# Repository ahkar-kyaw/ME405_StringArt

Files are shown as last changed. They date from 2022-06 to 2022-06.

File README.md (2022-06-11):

<!---
<img src="media/1.gif" alt="" width="200"/>
<img src="media/2.gif" alt="" width="200"/>
<img src="media/3.gif" alt="" width="200"/>
<img src="media/4.gif" alt="" width="200"/>

<img src="media/2.jpg" alt="" width="200"/>
<img src="media/3.jpg" alt="" width="200"/>
<img src="media/1.jpeg" alt="Cat_Original" width="200"/>
<img src="media/4.jpg" alt="Cat_String" width="200"/>
<img src="media/5.jpg" alt="" width="200"/>
<img src="media/6.jpg" alt="" width="200"/>
<img src="media/7.jpg" alt="" width="200"/>
<img src="media/8.jpg" alt="" width="200"/>
<img src="media/9.jpg" alt="" width="200"/>
<img src="media/10.jpg" alt="" width="200"/>

![](media/8.jpg)
![](media/9.jpg)
![](media/10.jpg)
-->

<p align="center">
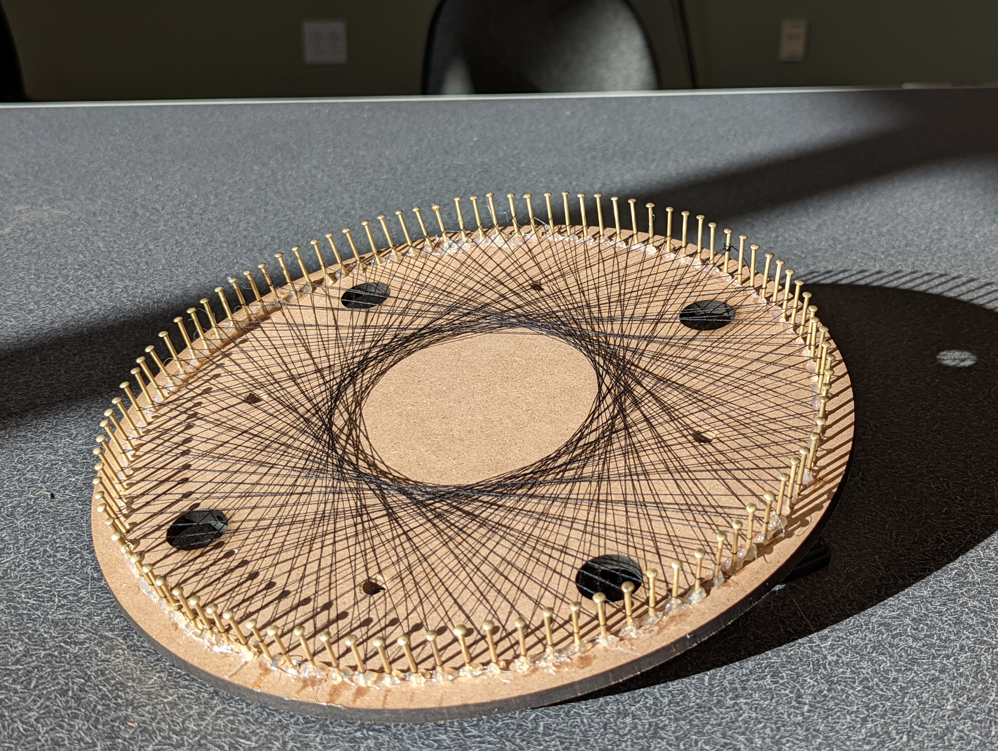
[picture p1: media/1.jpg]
  
</p>

<div align="center">
  <h1>String Art Machine</h1>
  <p><strong>By:</strong> Ahkar Kyaw, Elvis Tang</p>
</div>

In this tutorial we will learn how to build a machine that can replicate an image using strings. We built this machine for our ME405 class. It is still a work in progress with many rooms for improvement but we are very pleased with how far it has come and we are excited to share the project with you. 

# Introduction
String art, often referred to as pin-and-thread art, is a form of art that weaves colored string, wool, wire, or yarn between hammered nails to make geometric patterns. String art is not new and its origins go all the way back to the 19th century. It started off as an educational tool to introduce mathematical ideas to children but came back in the late 1960s as a decorative craft in a form of books and kits. 

Inspired by the beauty and complexity of this art style, we decided that we want to build a machine that can replicate any image using lines and recreate it physically in a form of string art. This was a very challenging project and due to time constraint, we were unable to perfect it to our desired standard. However, it works and we are thrilled to share our project with you. Hopefully you will be inspired to recreate a project like this yourself. 

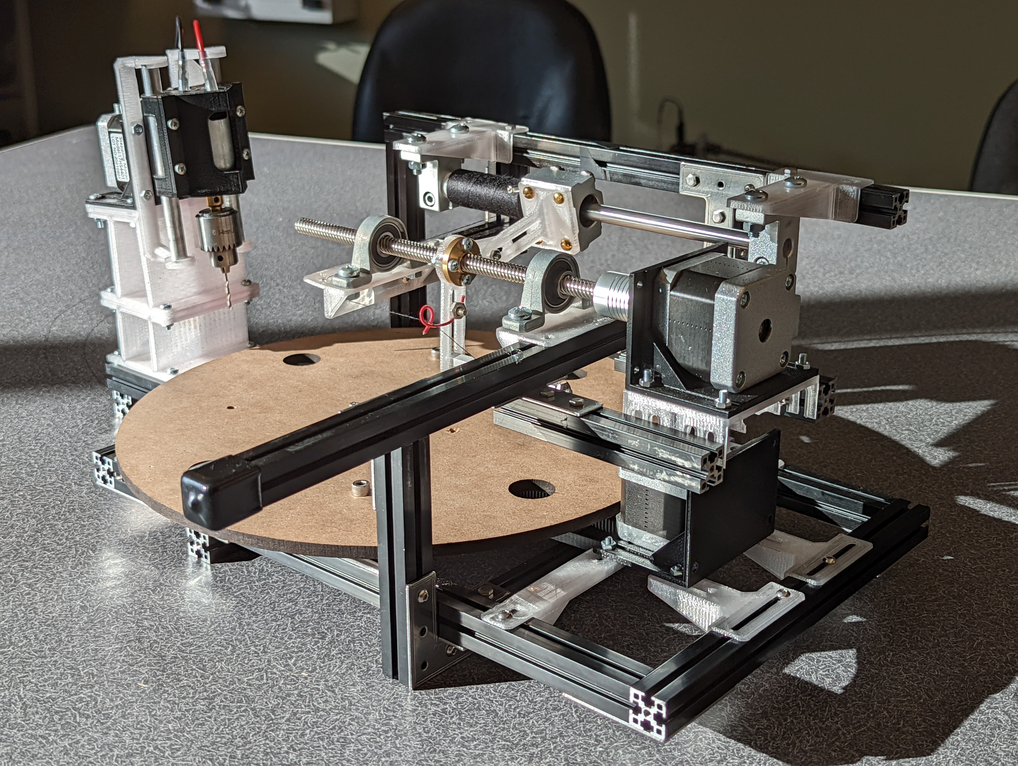
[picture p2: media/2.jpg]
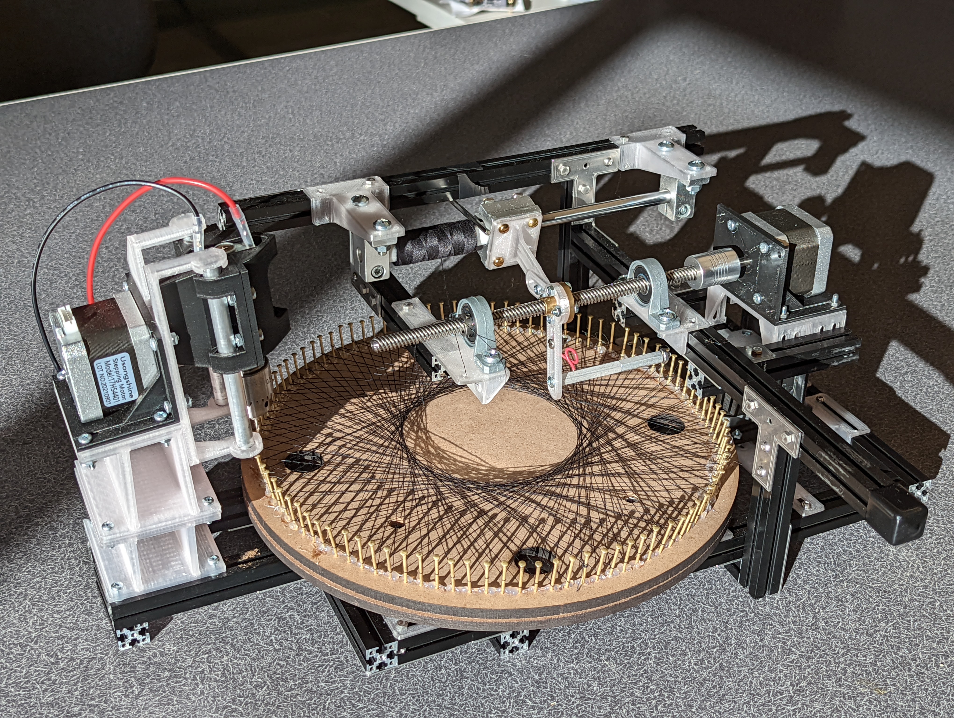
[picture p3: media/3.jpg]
|  | |
| --- | --- |

# Product Specification
## Hardware Components
| **Components** | **vender** | **Dimension** |
| :---:  | :---: | :---: |
| MDF board | [Amazon](https://www.amazon.com/dp/B07QWSTMWJ?ref_=cm_sw_r_cp_ud_dp_WGG48NSVNE196GH4DMZJ) | 14-in(L) x 11-in(W) x 0.25-in(T)|
| Nails | [Amazon](https://www.amazon.com/Projects-Antique-Repairing-Decorative-Accessories/dp/B082J2JXZD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) | 23mm(L) |
| String | [Amazon](https://www.amazon.com/dp/B07LC1YDVR?ref_=cm_sw_r_cp_ud_dp_Z0H458M8TY3VP6MC05YG) | 200m |
| 80/20 Aluminum Extrusion | [McMASTER-CARR](https://www.mcmaster.com/80//t-slotted-framing-rails/) | 20mm x 20mm |
| T8 Lead Screw Nut Set | [Amazon](https://www.amazon.com/dp/B07GV72326?ref_=cm_sw_r_cp_ud_dp_XBR2BX6C1A7YK6SPVKN0) | 200mm(L), 8mm(D) |

## Electronic Components
| **Components** | **Vender** | **Datasheet**  |
| :---:  | :---: | :--- |
| NUCLEO (STM32L476RG) | [MOUSER](https://www.mouser.com/ProductDetail/STMicroelectronics/NUCLEO-L476RG?qs=PRtH0mD6DWbM6mRV5DKjBQ%3D%3D) | https://www.st.com/resource/en/datasheet/stm32l476rg.pdf |
| Shoe of Brian | [OSHPARK](https://oshpark.com/shared_projects/e6X6OnYK) |  http://wind.calpoly.edu/ME405/doc/shoe_info.html |
| Mini Hand Drill DC Motor | [Amazon](https://www.amazon.com/AUTOTOOLHOME-Electric-Drill-Motor-Drills/dp/B01LZYWFE4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)| https://www.sears.com/autotoolhome-mini-dc-12v-electric-hand-drill-motor/p-A098205228 |
| NEMA 17 Stepper Motor | [Amazon](https://www.amazon.com/dp/B07QV1ZVJR?tag=rpantiques-20&linkCode=ogi&th=1) | http://www.autoflexible.com/file_upload/product/attach/NEMA%2017.pdf |
| LCD 1602 (I2C port) | [Amazon](https://www.amazon.com/dp/B019K5X53O?ref_=cm_sw_r_cp_ud_dp_NDRGXARM7KG02A7N59Y2) | http://www.handsontec.com/dataspecs/module/I2C_1602_LCD.pdf |
| TMC4210 | [MOUSER](https://www.mouser.com/ProductDetail/Trinamic/TMC4210-I?qs=TiOZkKH1s2TH5TqjeGBn1g%3D%3D) | https://www.trinamic.com/fileadmin/assets/Products/ICs_Documents/TMC4210_Datasheet_Rev.1.06.pdf |
| TMC2208 | [Amazon](https://www.amazon.com/Printer-TMC2208-Screwdriver-Controller-Ramps1-4/dp/B082LSQWZF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) | https://www.trinamic.com/fileadmin/assets/Products/ICs_Documents/TMC220x_TMC2224_datasheet_Rev1.09.pdf |

## Manufacturing / Machining Tools
| **Tool** | Source Files |
| :---:  | :---:  |
| 3D Printer | [ME405_StringArt/CAD Files/3D Printing/](https://github.com/AhKyaw/ME405_StringArt/tree/main/CAD%20Files/3D%20Printing) |
| Laser Cutter | [ME405_StringArt/CAD Files/Laser Cutting/](https://github.com/AhKyaw/ME405_StringArt/tree/main/CAD%20Files/Laser%20Cutting)  |

# System Design
## Mechanical Design
To begin with, let’s take a look at the mechanical components of this machine. The overall frame of this machine is made entirely out of 80/20 aluminum extrusion. The machines moves using 3 stepper motors and a DC motor with a drill attached to the tip. These motors are then mounted onto the frame using custom 3D printed parts. CAD files for these 3D printed parts can be found under Manufacturing - 3D Printer Source files. 

For the drawing board, we used a laser cut MDF board. The DXF file for laser cutting can be found under Manufacturing - Laser Cutter Source files. Once the board is cut, we attached it onto the 3D printed braket #4 and the lazy susan, which will be attached to the machine's frame. For the art canvas we want it to be easily removeable so we mounted another similar MDF board onto this existing platform using the pre-cut alignmnet holes. 

The full CAD model for the assembly of the machine can be found in the CAD folder under our GitHub Repository. 

<div align="center">
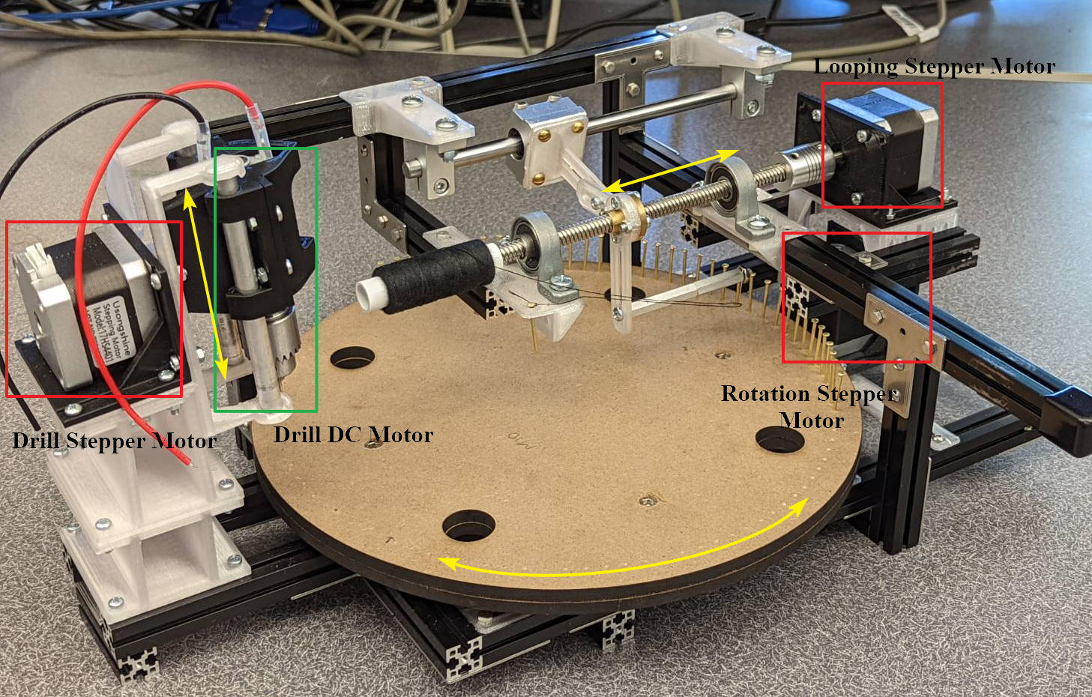
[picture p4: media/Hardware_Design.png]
Hardware_Design
  
</div>

## System Operating Procedure
<p>The figure below shows how the string art machine works. First, we need to convert the image to string art and generate its pin sequence via the Python file StringArt_Gen.py on our computer. After the pin sequence is generated, we will transfer this data to the Nucleo STM32 board. And based on the finite state machine and pin sequence, the Nucleo board will communicate with the motor driver through the SPI protocol and further control the motor to perform desired actions.</p>
<div align="center">
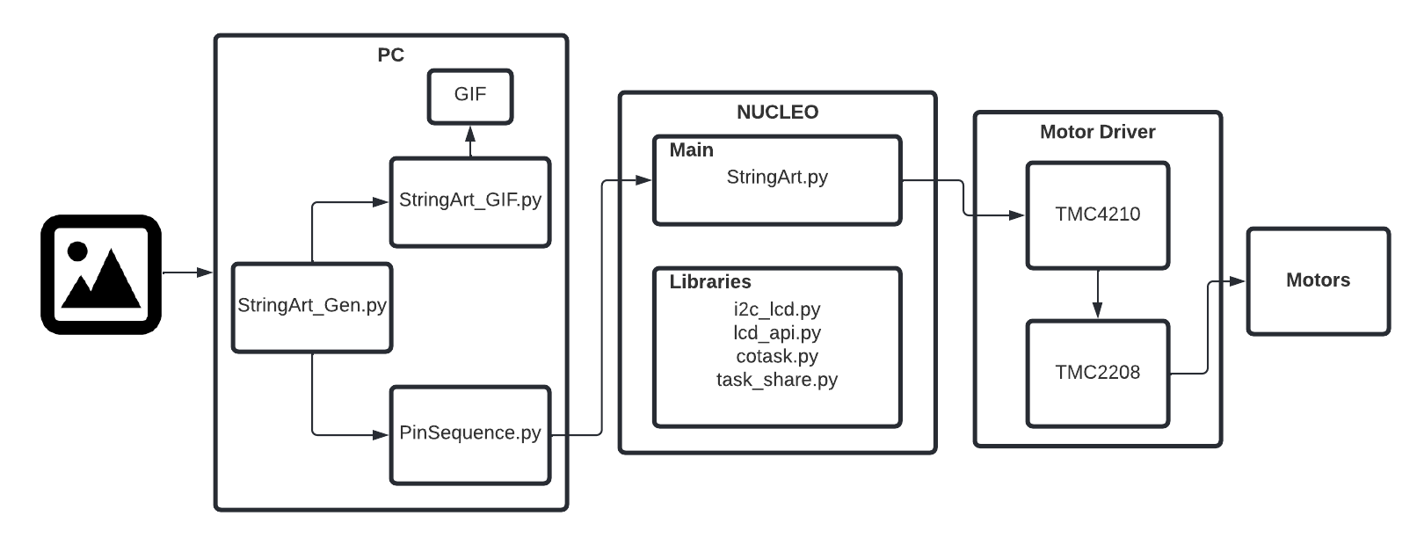
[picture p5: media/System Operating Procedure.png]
  
</div>

## Software Design
### String Art Generator
Our current StringArt_Gen.py file is heavily based on this github repository: [kaspermeerts/stringart.py](https://gist.github.com/kaspermeerts/781f0137b361b51224dcab722ae387b4), and also the knowledge in this paper: [String Art: Towards Computational Fabrication of String Images](https://www.dmg.tuwien.ac.at/geom/ig/publications/stringart/stringart.pdf).
<p>The two figures below show the image before and after string art conversion. And before we input the image into the string art generator, we need to crop the image into square shape to make the program run normally.</p>

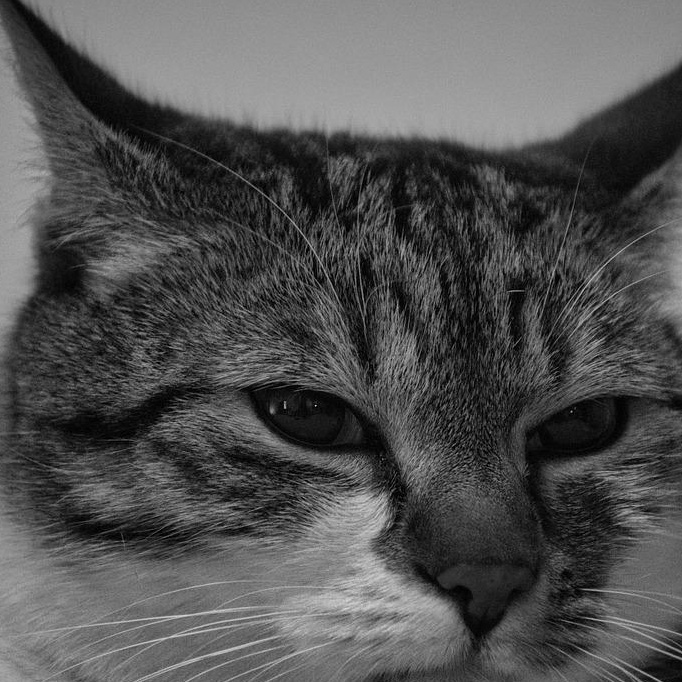
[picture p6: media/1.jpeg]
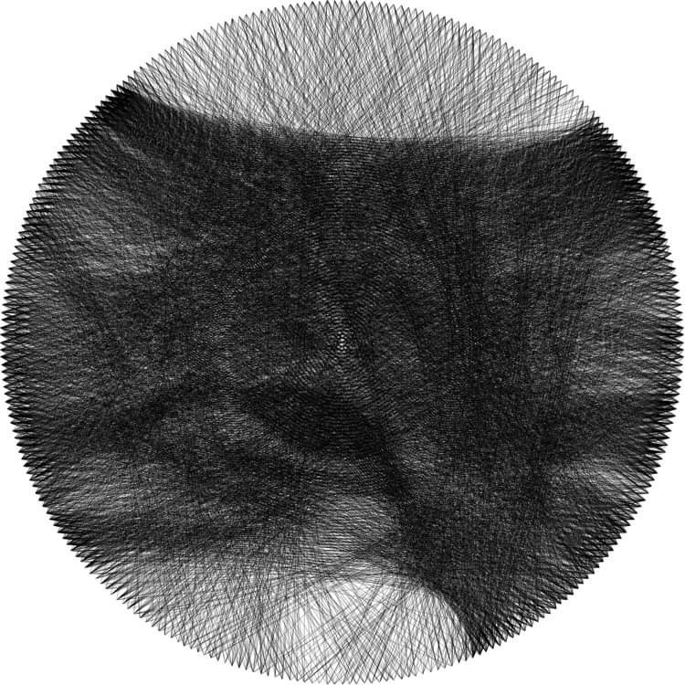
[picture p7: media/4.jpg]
|  |  |
| :---: |:---:|
| Original Image | String Art |

## Firmware Design
### Finite State Machine

<div align="center">
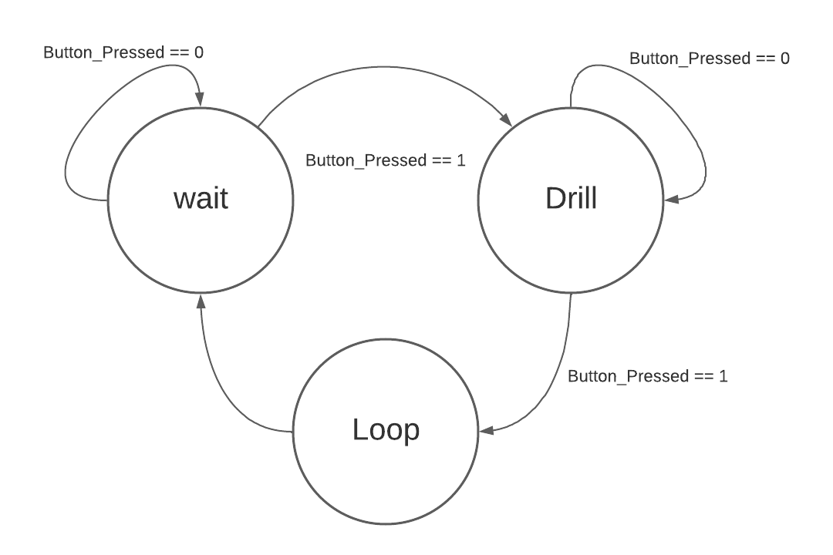
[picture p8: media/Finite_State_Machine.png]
  
</div>

There are a total of three states in this project. The first state is the wait state, in this state the system will initiate the motor setup and wait until the button is pressed. After pressing the button, the system enters the drilling state.</br>

In the drilling state, there are three subroutines, the board rotates to the desired pin, the drill stepper motor rolls the DC drilling motor down to drill holes in the board, and lifts the DC motor up after drilling to the desired depth. The system will loop through these subroutines until there are holes in all desired nail locations. Because we need to put the nails into the holes manually, the system will stay inside the drilling state till we finish inserting nails onto the board and press the button.</br> 

While finishing inserting the nails and pushing the button, the system will enter the looping state. There are four subroutines in the looping state, first, the board will rotate to the degree of desired nails + theta (theta is half of the degree difference between the two nails), and the needle will move outside the edge of the circle that constructs by the nails. After the needle moves outside the circle, the board will rotate to the degree of desired nails - theta. And the needle will move back inside the circle. These are the four subroutines that the system keeps looping through till the maximum number of lines is achieved.</br> 

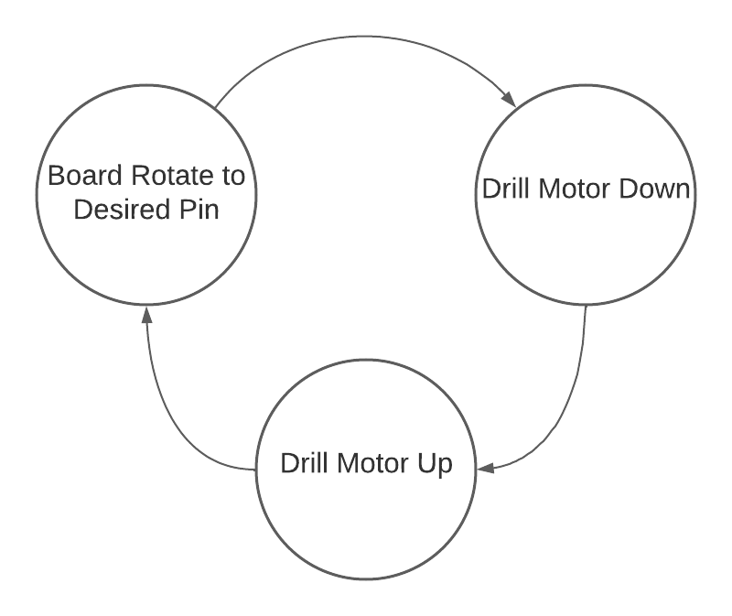
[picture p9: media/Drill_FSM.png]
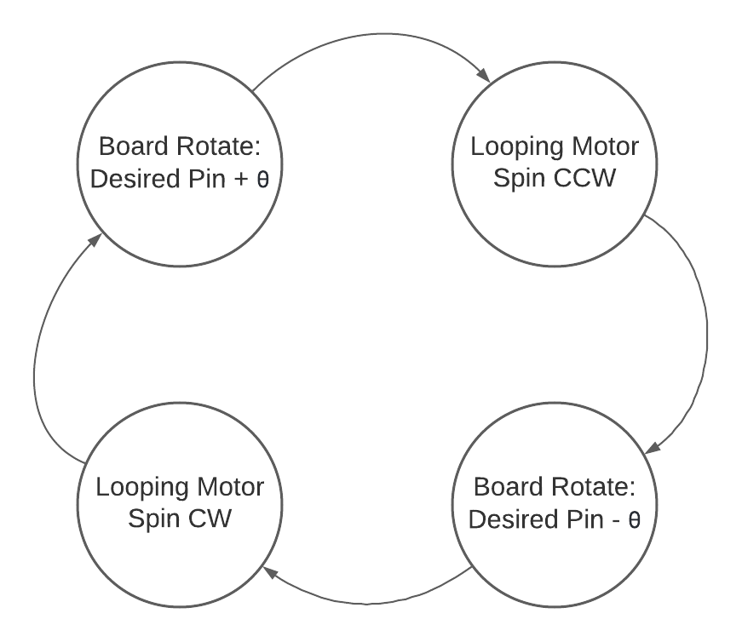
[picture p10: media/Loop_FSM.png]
|  |  |
| :---: |:---:|
| Drilling State | Loop State |

## Motor Control

We use TMC4210 and TMC2208 as our motion controller and motor driver. STM32 will communicate with the TMC4210 through the SPI protocols, and TMC4210 will generate respective steps and direction signals to TMC2208. After the TMC2208 receives those two signals, it will send the respective power to the motor and the motor will do the desired action.

<div align="center">
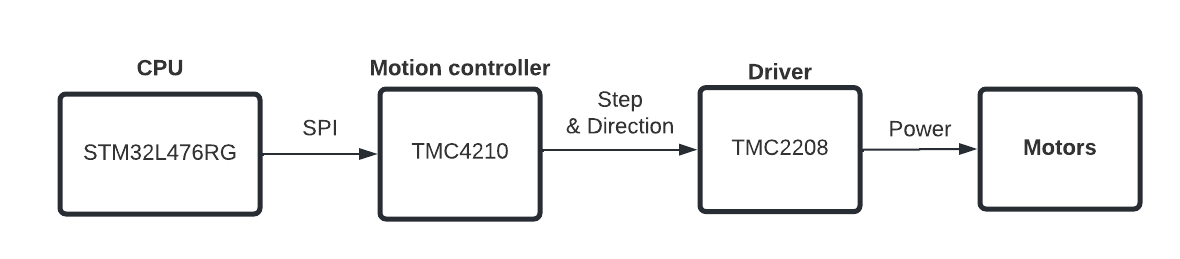
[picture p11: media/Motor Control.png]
  
</div>

# Results Demonstration
Here you will see our machine in action. There are 3 main stages to making a string art on this machine. First stage involves drilling holes for the nails to be slotted in and we call it the drilling stage. The second stage is where you manually put nails into these holes and attaching the string onto one of the nail. We call this stage a nailing stage. Last but not least, we have the looping stage where the needle move around and spin the board to loop the strings around the nails.

## Drilling
What you see below is a short timelapse of the machine drilling a hole and spinning the board around one step at a time. 



## Nailing
This is a very simple and manual stage where you manually put nails into each holes that the machine just drilled. Ideally, the holes will be deep enough such that they will be strong and stable to withstand the tension created by the string. However, we bought a quarter inch MDF board for our project and it turns out, quarter inch was insufficient to withstand the load so we had to go an extra step and used some hot-glue to make the base contact a little stronger. After all the nails are slotted in, tie the end of the string onto one of the nail and position this nail directly under the needle. Ideally, we want to use limit switches so that the alignment process is automated. For now, we manually aligned the first nail with the needle tip. 

## Looping
### Without Interference
The gif you see below is a short timelapse of the machine looping the string around the nails without any human interference. It is pretty successful for the most part but as you can see, on the sixth loop, the nail was a little shorter than the designed height so the string slipped out, forcing us to restart the machine. 



### Mechanism
| This is a close up, real-time video showing how the needle and the strings are attached such that it can loop around the nail without getting tangled up.  |  | 
| :--- |:---|

# Challenges
Due to our lack of experience developing mechanical systems and budget constraint, most of the problems for the project arises in the mechanical side of the design. Since this is the first time developing such complex mechanical system for both of us, we spent too much time getting things right in the designing stage. We designed many of the parts from bottom up and that cost us a lot of time. By the time we finished a prototype to test with the program, we only have two weeks left. Therefore, we did not have much time to buy new parts and redesign the system to fix the problems. Ideally, we should have focused on getting the mechanical design ready using off the shelf components as early as possible so that we get more time to perfect the design. 

### Inconsistent Nail Height:<br>

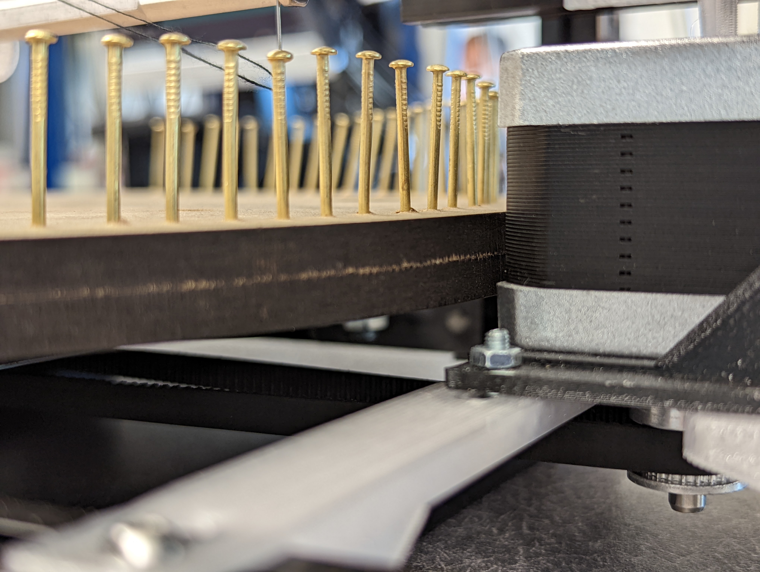
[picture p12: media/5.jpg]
|  | The first problem we encountered was the height inconsistency among the nails that we purchased. Even though we managed to drill all the holes to be exactly the same depth, the point of contact between each nail and the looping needle is different. Therefore, the string occasionally slip over the top if the nail is too short compared to others. To fix this problem, you need an alternative string feeding mechanism where the string is fed directly from the top instead of the side like what we have. This way, you the needle can loop the strings along a much lower plane without having to worry about the string getting tangled up. |
| --- |:---|

### String Getting Tangled Up:<br>
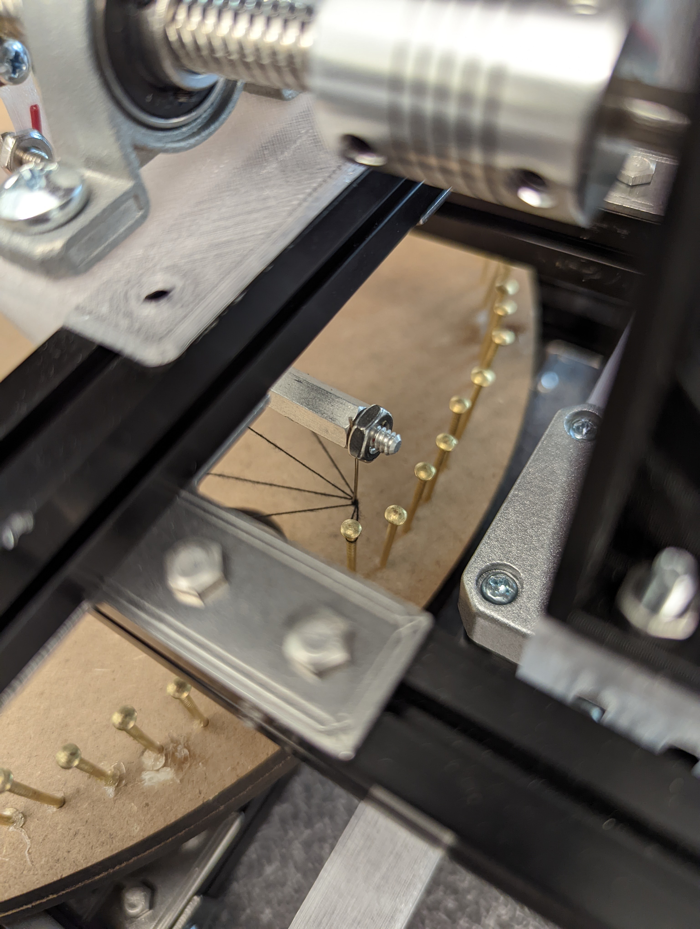
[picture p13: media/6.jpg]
|  | The second problem we encountered was with regards to the string getting tangled up after looping around the nail. There are two main reasons for why this happen. First is due to the lack of tension and retraction system for the string. This causes the string to droop down after the needle pulls the string to loop around the nail everytime. When the board rotates after, the loose part causes the strings to get tangled up. To fix this problem, you could modify the string feeding system so that it goes through several pulley to maintain the tension in the string. You could also add a retraction system to the spool of string so that it will prevent the string from drooping down after pulling it too far. The second reason is due to the nails not being slanted enough. We knew all along that if all the strings loop around along the same height, it will cause them to crash with each other causing the stings to get tangled up when rotating the board. Therefore, we tiltted the drill bit to be at a 5 degrees angle from the vertical, hoping that the slope will cause the strings to slide down the nail after each loop. However, the slope was not steep enough, causing the strings to get tangled up. For future development, the drill should be angled at least 10 degrees from the vertical. |
| --- |:---|

### Insufficient Nail Depth:<br>
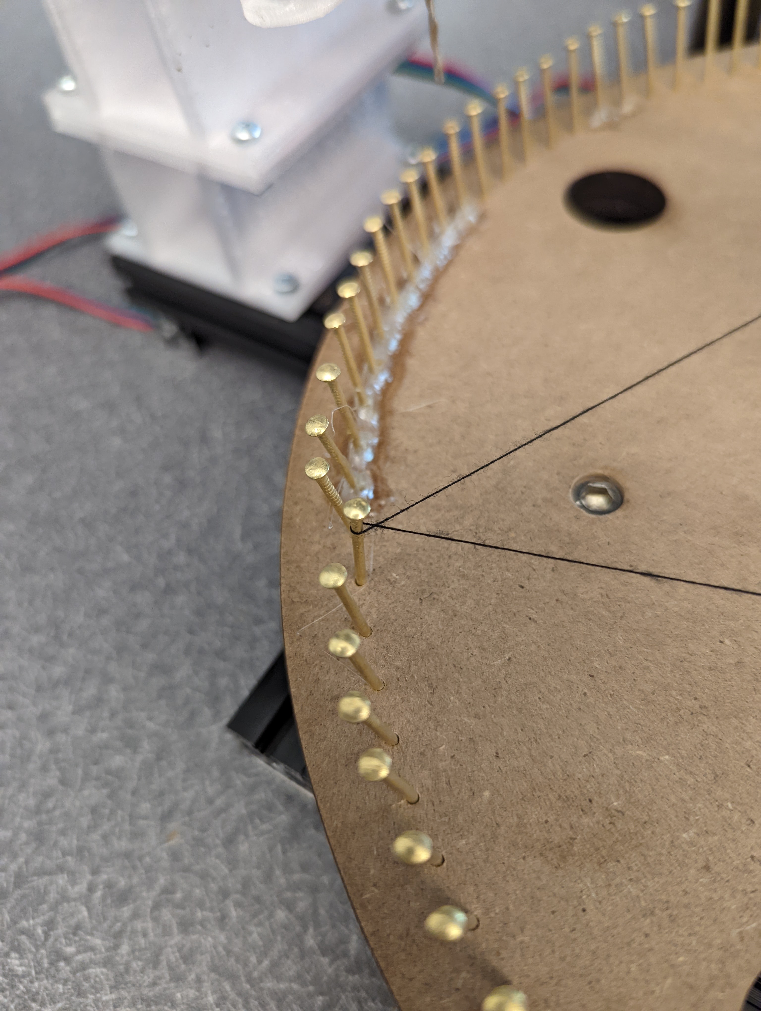
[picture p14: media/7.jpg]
|  | The third problem we encountered was with regards to the having insufficient nail depth. We bought a quarter inch MDF board thinking it was sufficient depth for the nails. However, quarter inch was too shallow and the nails were not pinned deep enough so when the tension in the string gets high, the torque causes the nails to get ejected from the hole. Therefore for this project, we used some hot-glue to pin it to the base. A permanent solution to this problem would be to use at least a half inch MDF board. |
| --- |:---|

# Full Run (With Intervention)
In the end, we managed to do a full run on the machine with a little bit of human intervention. We slowed the speed of string looping so that there is sufficient time for us to make sure the string is looped correctly. Most of the time, we used a small tweezers to push the string down on the nail so that they do not end up interfering with one another. Occasionally, we have to manually loop the strings onto the nail. This was the result of some nails being not long enough to reach the design height as mentioned previously. 

<div align="center">
  Machine in Action (with intervention)
</div>

# Conclusion
Overall, it was a very fun project and we learned a lot from this experience. The machine still has many rooms for improvement and we are planning to continue working on it even after the class ends. We hope you like the project and hopefully it inspired you to build one of your own.

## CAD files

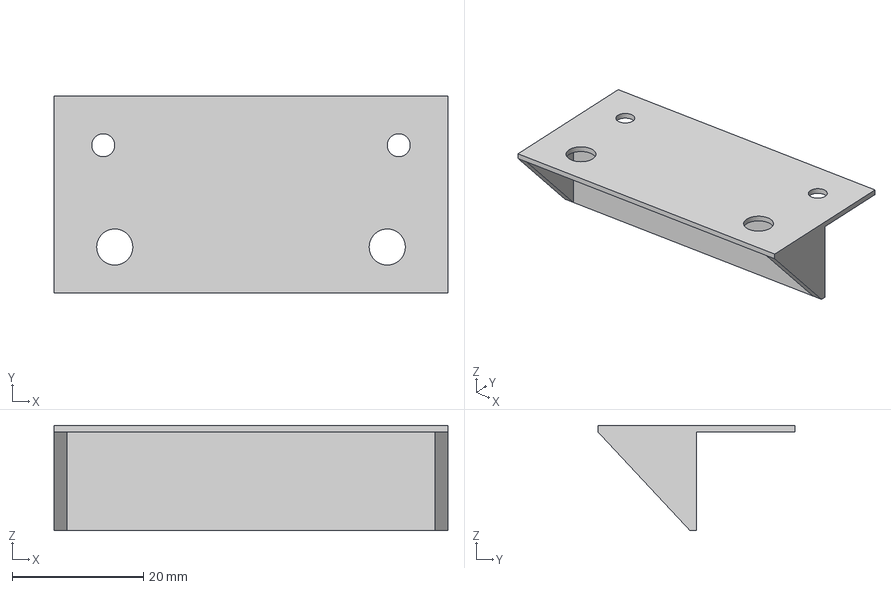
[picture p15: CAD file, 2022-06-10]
CAD Files/3D Printing/Bracket 7.step
60.0 x 30.0 x 16.0 mm

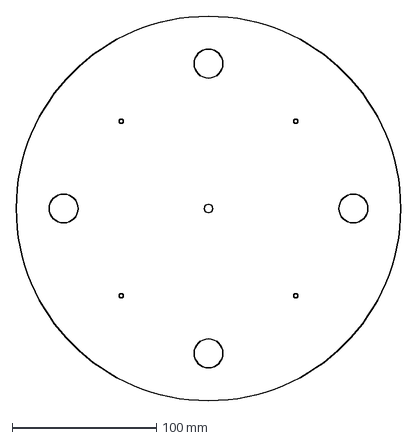
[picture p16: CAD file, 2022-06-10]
CAD Files/Laser Cutting/BasePlate.dxf
266.7 x 266.7 mm

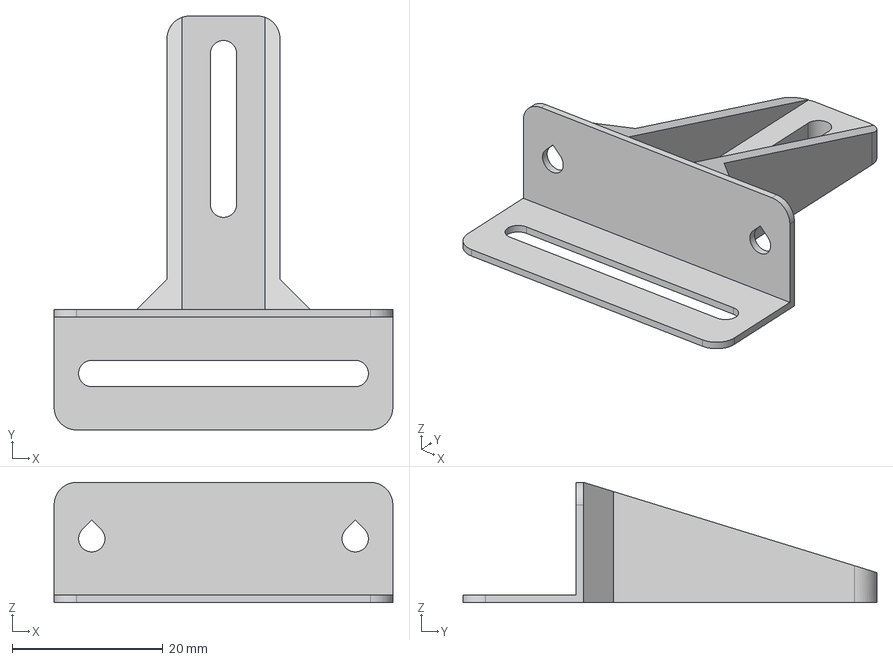
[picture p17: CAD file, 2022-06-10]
CAD Files/3D Printing/Bracket 1.step
45.0 x 55.0 x 16.0 mm

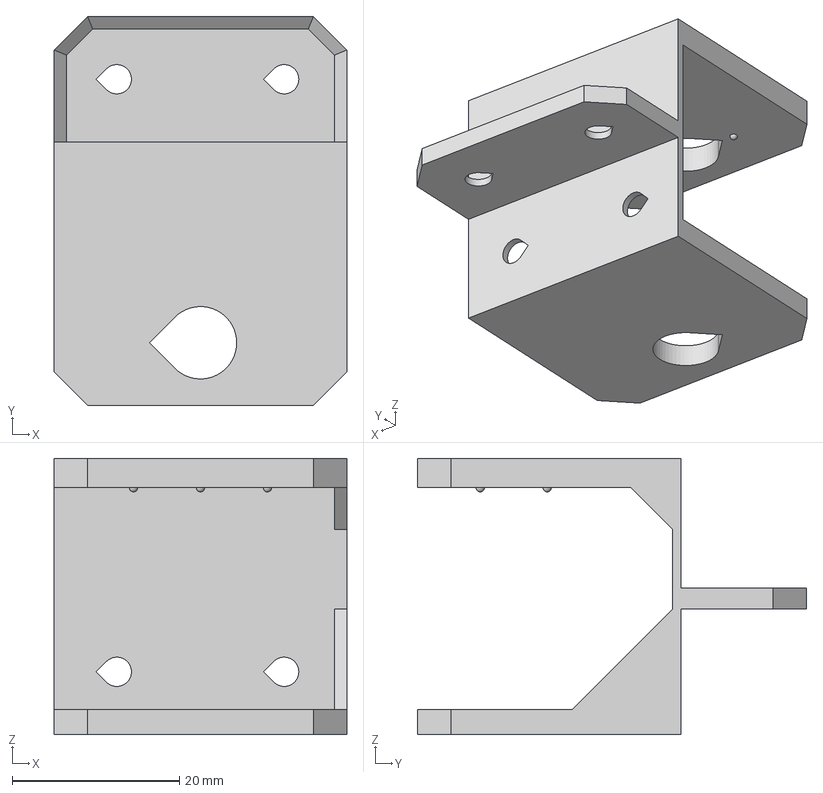
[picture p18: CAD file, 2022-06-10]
CAD Files/3D Printing/Bracket 3.step
35.0 x 46.5 x 33.0 mm

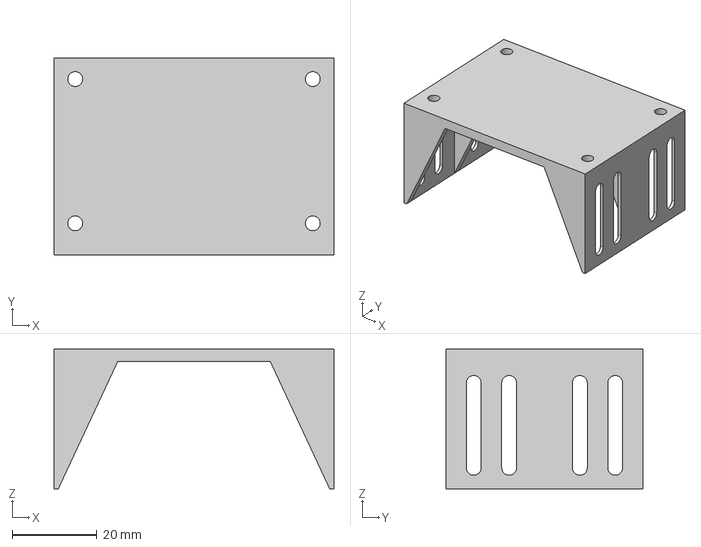
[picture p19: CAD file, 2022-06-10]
CAD Files/3D Printing/Bracket 5.step
66.0 x 46.5 x 33.0 mm

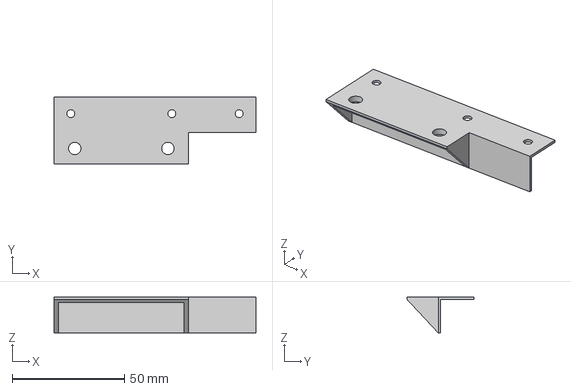
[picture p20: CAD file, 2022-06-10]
CAD Files/3D Printing/Bracket 6.step
90.0 x 30.0 x 16.0 mm

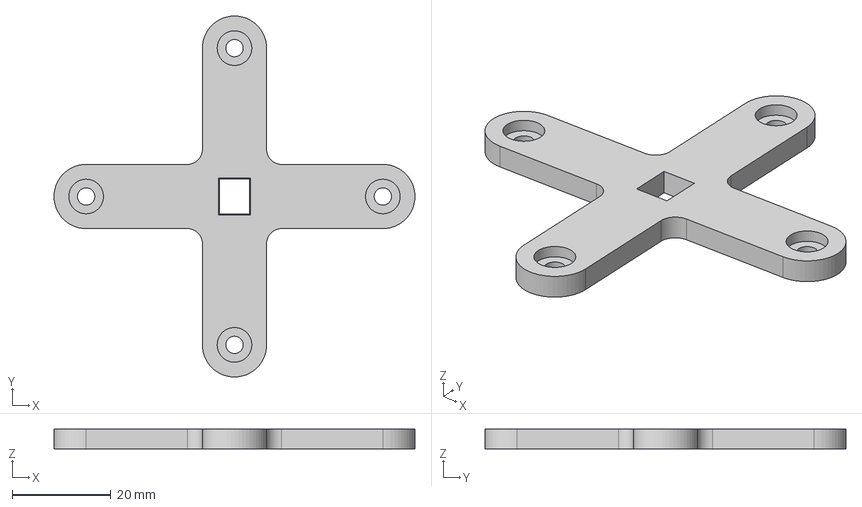
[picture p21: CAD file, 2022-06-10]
CAD Files/3D Printing/Bracket 4.step
73.0 x 73.0 x 4.00 mm

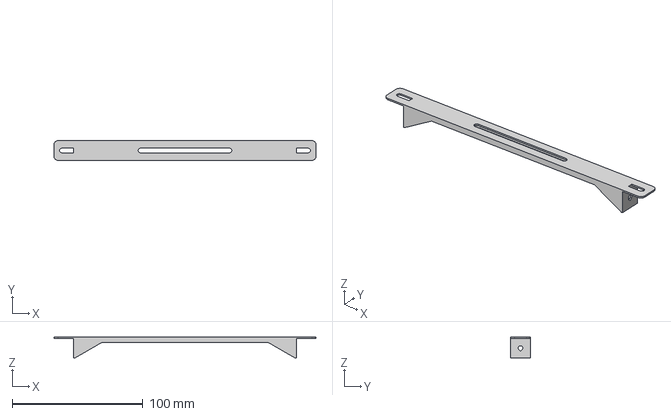
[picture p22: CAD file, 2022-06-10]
CAD Files/3D Printing/Bracket 2.step
200.0 x 15.0 x 16.0 mm

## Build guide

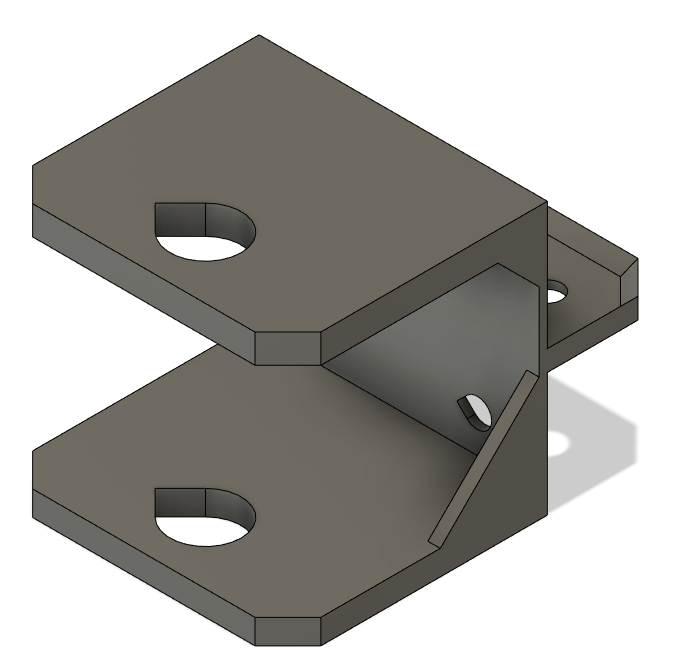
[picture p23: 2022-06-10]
CAD Files/3D Printing/Bracket 3.png

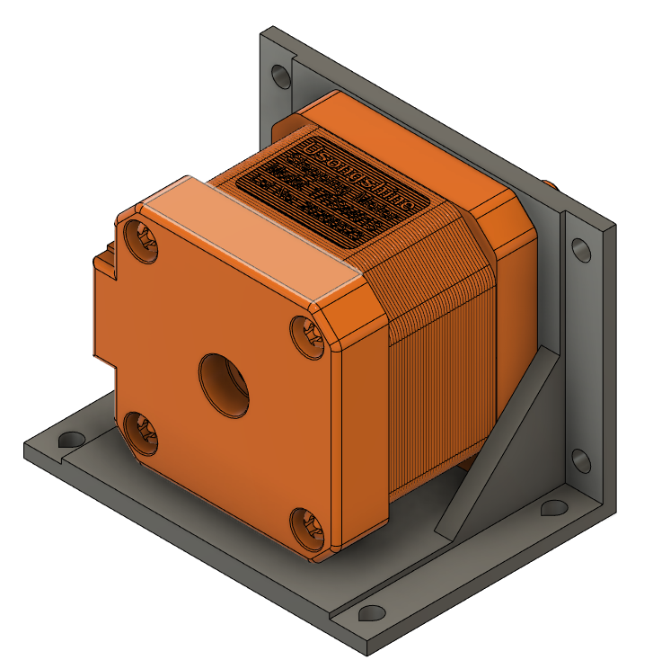
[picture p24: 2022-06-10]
CAD Files/3D Printing/Stepper Motor Mount.png

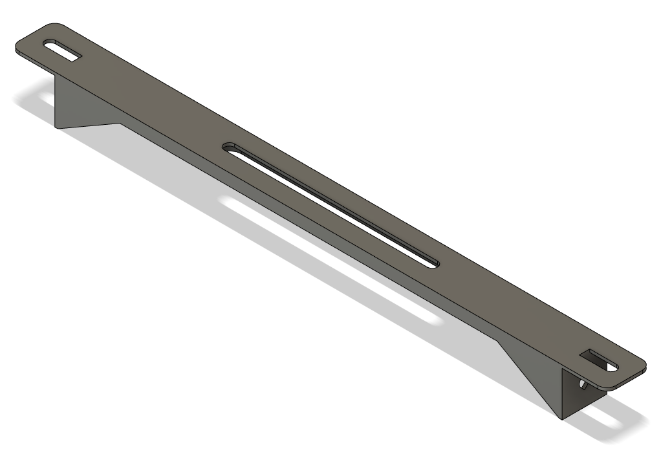
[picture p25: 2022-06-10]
CAD Files/3D Printing/Bracket 2.png

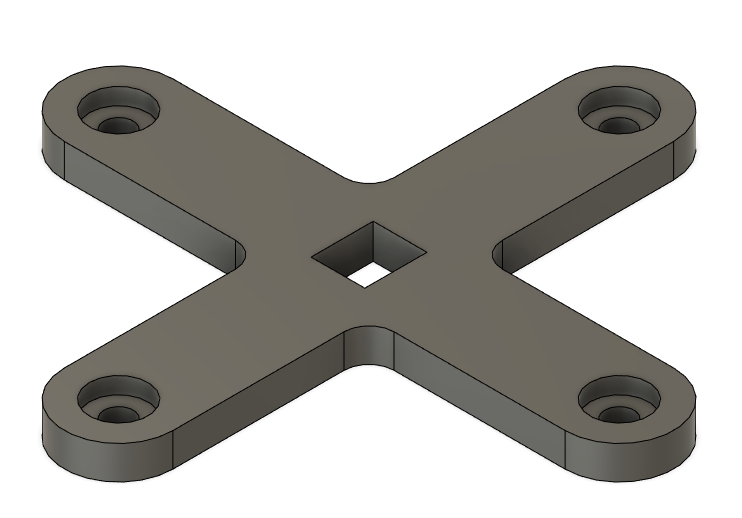
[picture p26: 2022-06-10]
CAD Files/3D Printing/Bracket 4.png

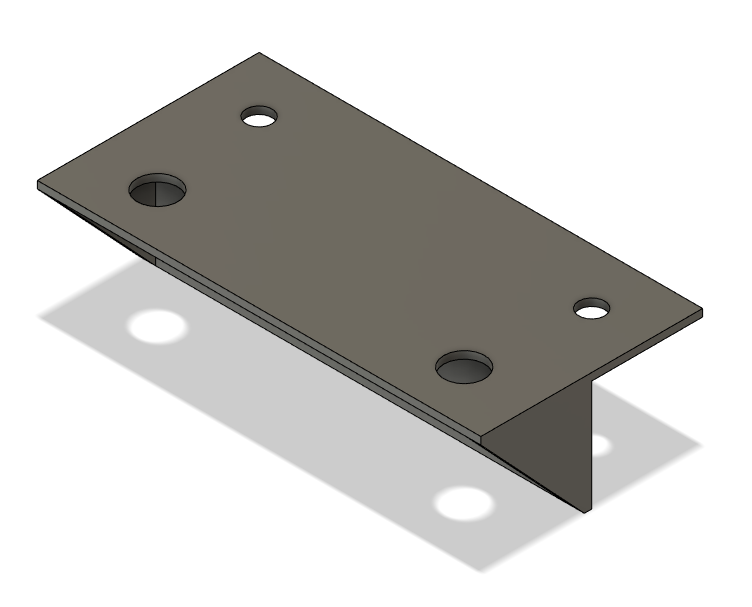
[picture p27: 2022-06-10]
CAD Files/3D Printing/Bracket 7.png

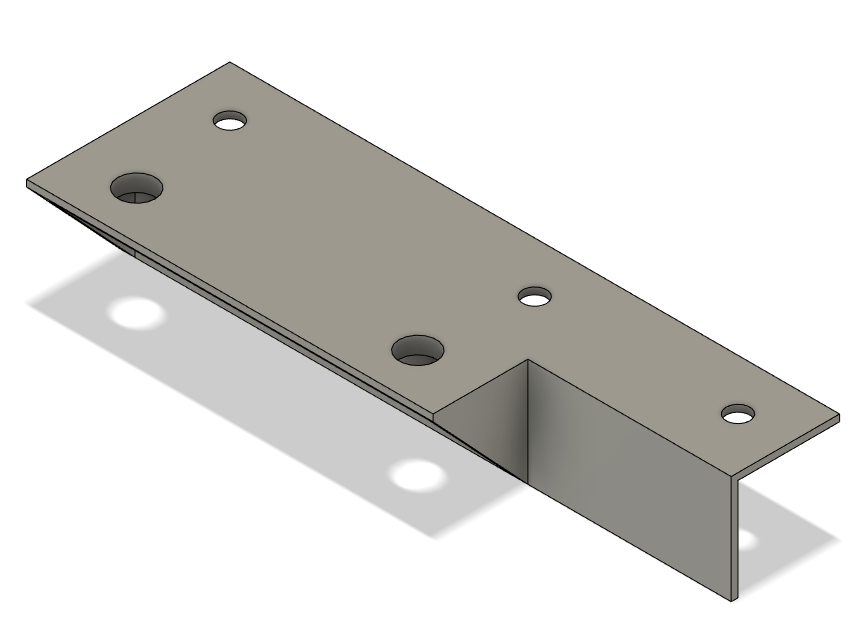
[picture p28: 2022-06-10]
CAD Files/3D Printing/Bracket 6.png

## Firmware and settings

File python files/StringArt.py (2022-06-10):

import pyb
from pyb import Pin, Timer, ExtInt, repl_uart, UART, delay, SPI
import math
import cotask
import task_share
import machine
from machine import Pin, SoftI2C
from lcd_api import LcdApi
from i2c_lcd import I2cLcd
from MS_Paint_Circles import pin_sequence

def I2C_init(PIN, AF):
    PIN_name = str(PIN[1:])
    PIN = Pin(PIN_name, mode=Pin.AF_PP, af=1)
    return PIN

def clock_init(PIN, AF, tim_num, ch_num):
    PIN_name = str(PIN[1:])
    PIN = Pin(PIN_name, mode=Pin.AF_PP, af=1)
    tim = Timer(tim_num, prescaler=0, period=3)
    clk = tim.channel(ch_num, mode=Timer.PWM, pin=PIN, pulse_width=2)
    return PIN

class TMC4210:

    def __init__ (self, EN_PIN, CS_PIN):
        self.EN_PIN = EN_PIN
        self.CS_PIN = CS_PIN

    def EN_init(self): # Active low
        PIN_name = str(self.EN_PIN[1:])
        self.EN_PIN = Pin(PIN_name, mode=Pin.OUT_PP, value=1)
        self.EN_PIN.low() # Enable TMC2208_1
        return self.EN_PIN

    def CS_init(self): # Active low
        PIN_name = str(self.CS_PIN[1:])
        self.CS_PIN = Pin(PIN_name, mode=Pin.OUT_PP, value=1)
        return self.CS_PIN

    def SPI_SendRecv(self,dataSend):
        dataRecv = bytearray(4)
        self.CS_PIN.low()
        spi.send_recv(dataSend, dataRecv, timeout=5000)
        self.CS_PIN.high()
        return dataRecv

    def byteIndex(self, MSB, LSB):

        dataLength = MSB - LSB + 1                   # calculate the data length
        ByteLength = math.ceil(dataLength/8)         # calculate the byte length

        mod = dataLength%8                           # calculate modulos for later check of how many bytes data has crossed
        if mod == 0:
            mod = 8
        if (LSB%8) > (8-mod):                        # Check how many bytes data has crossed
            ByteLength += 1

        stByte = 3 - math.floor(LSB/8)               # Define start byte index based on MSB first
        endByte = stByte - ByteLength + 1            # Define end byte index based on MSB first
        byteIndex = list(range(stByte,endByte-1,-1)) # store the bytes data has crossed in a list

        return byteIndex


    def setVal(self, RegAddr, RW, MSB, LSB, SetVal):

        # Register[0]: Addr
        Register = bytearray(4)
        Register[0] |= ((RegAddr << 1) | RW)

        # Whether it's a read or write operation
        if RW == READ:
            print('READ')
            pass

        elif RW == WRITE:
            print('WRITE')
            index = self.byteIndex(MSB,LSB)
            SetVal = SetVal << LSB

            while(len(index)):
                if(index[0]==1):
                    Register[1] |= ((SetVal >> 16) & 0xff)

                elif(index[0]==2):
                    Register[2] |= ((SetVal >> 8) & 0xff)

                elif(index[0]==3):
                    Register[3] |= ((SetVal >> 0) & 0xff)

                index.pop(0)

        dataRecv = self.SPI_SendRecv(Register)
        return dataRecv

    def setPulseRampDiv(self, maxSpeed, maxAccel,f_CLK):
        pulseDiv = math.floor(math.log2(f_CLK*2047/(abs(maxSpeed)*2048*32)))
        rampDiv = math.floor(math.log2(f_CLK*f_CLK*2047/(abs(maxAccel)*2**(pulseDiv+29))))

        PulseRampDiv = [pulseDiv,rampDiv]

        return PulseRampDiv

    def setPmulPdiv(self, maxAccel,PulseRampDiv):
        p = maxAccel/(128*2^(PulseRampDiv[1]-PulseRampDiv[0]))
        p_reduced = p * 0.99

        for pdiv in range(14):
            pmul = p_reduced * 9 * 2 ** pdiv - 128
            if 0 <= pmul <= 127:
                pm = pmul + 128
                pd = pdiv

        PmulPdiv = [pm, pd]

        return PmulPdiv

    def motor_init(self,vmin,vmax):

        # initialize chip select (EN, CS)
        self.EN_init()
        self.CS_init()

        # Read from TYPE VERSION register
        print('typeVer_R')
        typeVer_R = self.setVal(RegisterAddress["TYPE_VER"], READ, 23, 0, -1)

        # Enable Step/Direction by setting en_sd bit 1 in IF_CONFIG register
        print('en_sd_W')
        en_sd_W = self.setVal(RegisterAddress["IF_CONFIG"], WRITE, 5, 5, 1)

        # Set the velocity parameters V_MIN and V_MAX
        print('V_MIN_W')
        V_MIN_W = self.setVal(RegisterAddress["V_MIN"], WRITE, 10, 0, vmin)
        print('V_MAX_W')
        V_MAX_W = self.setVal(RegisterAddress["V_MAX"], WRITE, 10, 0, vmax)

        # Set the clock pre-drivers PULSE_DIV and RAMP_DIV
        PulseDiv_RampDiv = self.setPulseRampDiv(2000, 10, 20e6)
        PRD_value = (PulseDiv_RampDiv[0] << 4 | PulseDiv_RampDiv[1])

        print('PULSE_RAMP_DIV_W')
        PulseDiv_W = self.setVal(RegisterAddress["PULSE_RAMP_DIV"], WRITE, 15, 8, PRD_value)

        print("PulseDiv: " + str(PulseDiv_RampDiv[0]))
        print("RampDiv: " + str(PulseDiv_RampDiv[1]) + "\n")

        # Set the A_MAX  with a valid pair of PMUL and PDIV
        print('A_MAX_W')
        A_MAX_W = self.setVal(RegisterAddress["A_MAX"], WRITE, 10, 0, 10)

        # Set Pmul & Pdiv
        PMUL_PDIV = self.setPmulPdiv(10, PulseDiv_RampDiv)
        PMD_value = (round(PMUL_PDIV[0]) << 8 | PMUL_PDIV[1])
        print('PMUL_PDIV_W')
        PMUL_PDIV_W = self.setVal(RegisterAddress["PMUL_PDIV"], WRITE, 14, 0, PMD_value)
        print("PMUL: " + str(PMUL_PDIV[0]))
        print("PDIV: " + str(PMUL_PDIV[1]))

        # Set Ramp_mode
        RM_W = self.setVal(RegisterAddress["R_M"], WRITE, 1, 0, 0)

        # Choose the reference switch configuration. Set mot1r to 1 for a left and a right reference
        # switch. If this bit is not set and the right switch is not to be used, pull REF_R to GND.
        print('mot1r_W')
        mot1r_W = self.setVal(RegisterAddress["MOT1R"], WRITE, 21, 21, 1)

    def motor_Calib(self):
        # Set the position parameters X_TARGET and X_ACTUAL
        # Calibrating: Before overwriting X_ACTUAL choose velocity_mode or hold_mode
        RM_W = self.setVal(RegisterAddress["R_M"], WRITE, 1, 0, 1)
        print('X_ACTUAL_W')
        X_ACTUAL_R = self.setVal(RegisterAddress["X_ACTUAL"], WRITE, 23, 0, 0)

    def motor_Control(self, usteps):
        # Set back to Ramp_mode
        RM_W = self.setVal(RegisterAddress["R_M"], WRITE, 1, 0, 0)
        print('X_TARGET_W')
        X_TARGET_W = self.setVal(RegisterAddress["X_TARGET"], WRITE, 23, 0, usteps) # nema 17 step/revolution : 1600
                                                                                    # MITSUMI step/revolution : 384

def Start_Button(tim):
    Start_flag.put(True)

button_int = ExtInt(Pin.cpu.C13, ExtInt.IRQ_FALLING, Pin.PULL_NONE, Start_Button)

def Task_StringArt():

    WAIT = 0
    DRILL = 1
    LOOP = 2
    CS = 0

    while True:
        if CS == WAIT:
            lcd.putstr("PUSH THE Button")
            delay(1000)
            lcd.clear()
            if(Start_flag.get()):
                print('CS = WAIT & INIT, NS = DRILL')
                lcd.clear()
                lcd.putstr("WAIT&INIT STATE")
                delay(1000)
                # MOTOR INIT
                Motor_Str = TMC4210('PB0','PC0')
                Motor_Str.motor_init(1800,2000)

                Motor_Rot = TMC4210('PC2','PC3')
                Motor_Rot.motor_init(1800,2000)

                Motor_Drill = TMC4210('PB1','PC1')
                Motor_Drill.motor_init(200,200)
                Start_flag.put(False)

                CS = DRILL

            else:
                print('CS = WAIT & INIT, NS = WAIT & INIT')
                CS = WAIT

        elif CS == DRILL:
            print('CS = DRILL, NS = LOOP')
            lcd.clear()
            lcd.putstr("DRILL STATE")
            Motor_Rot.motor_Calib()
            Motor_Drill.motor_Calib()
            p = 0
            for i in range(0):
                Motor_Rot.motor_Control(p)
                p += round(3*1600/pinNum)
                delay(2000)
                Motor_Drill.motor_Control(765)
                delay(6000)
                Motor_Drill.motor_Control(450)
                delay(2000)
            Motor_Drill.motor_Control(0)
            CS = LOOP

        elif CS == LOOP:
            print('CS = LOOP, NS = WAIT')
            lcd.clear()
            lcd.putstr("LOOP STATE")
            for i in range(len(pin_sequence)):
                Motor_Rot.motor_Control(round((3*1600/pinNum)* pin_sequence[i]) + round(3*1600/(pinNum*1.5)))
                delay(4000)
                Motor_Str.motor_Control(2000)
                delay(4000)
                Motor_Rot.motor_Control(round((3*1600/pinNum)* pin_sequence[i]) - round(3*1600/(pinNum*2)))
                delay(4000)
                Motor_Str.motor_Control(-1500)
                delay(4000)
                while (not Start_flag.get()):
                    print('Press the button')
                Start_flag.put(False)
            CS = WAIT
        else:
            print('OHHHHHHHH NOOOOO')
            pass

        yield (0)

if __name__ == "__main__":

    # constants
    WRITE = 0
    READ = 1
    pinNum = 100

    I2C_ADDR = 0x27
    totalRows = 2
    totalColumns = 16

    # dictionary
    RegisterAddress = {
        "X_TARGET":0,
        "X_ACTUAL":1,
        "V_MIN":2,
        "V_MAX":3,
        "V_TARGET":4,
        "V_ACTUAL":5,
        "A_MAX":6,
        "A_ACTUAL":7,
        "PMUL_PDIV":9,
        "R_M":10,
        "PULSE_RAMP_DIV":12,
        "IF_CONFIG":52,
        "TYPE_VER":57,
        "MOT1R":63,
    }

    # initialize fclk
    PB3 = clock_init('PB3', 1, 2, 2)

    # initialize serial peripheral interface
    spi = SPI(2, SPI.MASTER, 1250000, polarity=1, phase=1)

    # initialize I2C
    SCL = I2C_init('PB8', 4)
    SDA = I2C_init('PB9', 4)
    i2c = machine.SoftI2C(sda=SDA, scl=SCL)
    lcd = I2cLcd(i2c, I2C_ADDR, totalRows, totalColumns)

###########################    TASK INIT STARTS   ##############################
    Start_flag = task_share.Share ('h', thread_protect = False, name = "Start Flag")

    Task_StringArt = cotask.Task (Task_StringArt, name = 'Task_StringArt', priority = 1, period = 400, profile = True, trace = False)

    # Add Task_Comms to the task list
    cotask.task_list.append (Task_StringArt)

    # Set up the task scheduler
    vcp = pyb.USB_VCP ()
    while not vcp.any ():
        cotask.task_list.pri_sched ()

    vcp.read ()

    print ('\n' + str (cotask.task_list))
    print (task_share.show_all ())
    print (Task_Comms.get_trace ())
    print ('\r\n')
###########################    TASK INIT ENDS   ##############################

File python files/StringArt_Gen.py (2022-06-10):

import collections
import math
import os
import cv2
import numpy as np
import time

MAX_LINES = 350
N_PINS = 100
MIN_LOOP = 20               # To avoid getting stuck in a loop
MIN_DISTANCE = 20           # To avoid very short lines
LINE_WEIGHT = 15            # Tweakable parameter
FILENAME = "MS_Paint_Circles.png"
SCALE = 25                  # For making a very high resolution render, to attempt to accurately gauge how thick the thread must be
HOOP_DIAMETER = 0.625       # To calculate total thread length

tic = time.perf_counter()

img = cv2.imread(FILENAME, cv2.IMREAD_GRAYSCALE)

# Didn't bother to make it work for non-square images
assert img.shape[0] == img.shape[1]
length = img.shape[0]

def disp(image):
    cv2.imshow('image', image)
    cv2.waitKey(0)
    cv2.destroyAllWindows()

# Cut away everything around a central circle
X,Y = np.ogrid[0:length, 0:length]
circlemask = (X - length/2) ** 2 + (Y - length/2) ** 2 > length/2 * length/2
img[circlemask] = 0xFF

pin_coords = []
center = length / 2
radius = length / 2 - 1/2

# Precalculate the coordinates of every pin
for i in range(N_PINS):
    angle = 2 * math.pi * i / N_PINS
    pin_coords.append((math.floor(center + radius * math.cos(angle)),
                       math.floor(center + radius * math.sin(angle))))

line_cache_y = [None] * N_PINS * N_PINS
line_cache_x = [None] * N_PINS * N_PINS
line_cache_weight = [1] * N_PINS * N_PINS # Turned out to be unnecessary, unused
line_cache_length = [0] * N_PINS * N_PINS

print("Precalculating all lines... ", end='', flush=True)

for a in range(N_PINS):
    for b in range(a + MIN_DISTANCE, N_PINS):
        x0 = pin_coords[a][0]
        y0 = pin_coords[a][1]

        x1 = pin_coords[b][0]
        y1 = pin_coords[b][1]

        d = int(math.sqrt((x1 - x0) * (x1 - x0) + (y1 - y0)*(y1 - y0)))

        #d = max(abs(y1-y0), abs(x1-x0)) inf-norm
        
        # A proper (slower) Bresenham does not give any better result *shrug*
        xs = np.linspace(x0, x1, d, dtype=int)
        ys = np.linspace(y0, y1, d, dtype=int)

        line_cache_y[b*N_PINS + a] = ys
        line_cache_y[a*N_PINS + b] = ys
        line_cache_x[b*N_PINS + a] = xs
        line_cache_x[a*N_PINS + b] = xs
        line_cache_length[b*N_PINS + a] = d
        line_cache_length[a*N_PINS + b] = d


print("done")

error = np.ones(img.shape) * 0xFF - img.copy()

img_result = np.ones(img.shape) * 0xFF
lse_buffer = np.ones(img.shape) * 0xFF    # Used in the unused LSE algorithm

result = np.ones((img.shape[0] * SCALE, img.shape[1] * SCALE), np.uint8) * 0xFF
line_mask = np.zeros(img.shape, np.float64) # XXX

line_sequence = []
pin = 0
line_sequence.append(pin)

thread_length = 0

last_pins = collections.deque(maxlen = MIN_LOOP)

for l in range(MAX_LINES):

    if l % 100 == 0:
        print("%d " % l, end='', flush=True)

        img_result = cv2.resize(result, img.shape, interpolation=cv2.INTER_AREA)

        # Some trickery to fast calculate the absolute difference, to estimate the error per pixel
        diff = img_result - img
        mul = np.uint8(img_result < img) * 254 + 1
        absdiff = diff * mul
        print(absdiff.sum() / (length * length))

    max_err = -math.inf
    best_pin = -1

    # Find the line which will lower the error the most
    for offset in range(MIN_DISTANCE, N_PINS - MIN_DISTANCE):
        test_pin = (pin + offset) % N_PINS
        if test_pin in last_pins:
            continue

        xs = line_cache_x[test_pin * N_PINS + pin]
        ys = line_cache_y[test_pin * N_PINS + pin]

        # Simple
        # Error defined as the sum of the brightness of each pixel in the original
        # The idea being that a wire can only darken pixels in the result
        line_err = np.sum(error[ys,xs]) * line_cache_weight[test_pin*N_PINS + pin]
        '''

        # LSE Unused
        goal_pixels = img[ys, xs]
        old_pixels = lse_buffer[ys, xs]
        new_pixels = np.clip(old_pixels - LINE_WEIGHT * line_cache_weight[test_pin*N_PINS + pin], 0, 255)

        line_err = np.sum((old_pixels - goal_pixels) ** 2) - np.sum((new_pixels - goal_pixels) ** 2)
        #LSE
        '''

        if line_err > max_err:
            max_err = line_err
            best_pin = test_pin

    line_sequence.append(best_pin)

    xs = line_cache_x[best_pin * N_PINS + pin]
    ys = line_cache_y[best_pin * N_PINS + pin]
    weight = LINE_WEIGHT * line_cache_weight[best_pin*N_PINS + pin]

    '''
    #LSE
    old_pixels = lse_buffer[ys, xs]
    new_pixels = np.clip(old_pixels - weight, 0, 255)

    lse_buffer[ys, xs] = new_pixels
    #LSE
    '''

    # Subtract the line from the error
    line_mask.fill(0)
    line_mask[ys, xs] = weight
    error = error - line_mask
    error.clip(0, 255)

    # Draw the line in the result
    cv2.line(result,
        (pin_coords[pin][0] * SCALE,      pin_coords[pin][1] * SCALE),
        (pin_coords[best_pin][0] * SCALE, pin_coords[best_pin][1] * SCALE),
        color=0, thickness=4, lineType=8)

    x0 = pin_coords[pin][0]
    y0 = pin_coords[pin][1]

    x1 = pin_coords[best_pin][0]
    y1 = pin_coords[best_pin][1]

    # Calculate physical distance
    dist = math.sqrt((x1 - x0) * (x1 - x0) + (y1 - y0)*(y1 - y0))
    thread_length += HOOP_DIAMETER / length * dist

    last_pins.append(best_pin)
    pin = best_pin

img_result = cv2.resize(result, img.shape, interpolation=cv2.INTER_AREA)

diff = img_result - img
mul = np.uint8(img_result < img) * 254 + 1
absdiff = diff * mul

print(absdiff.sum() / (length * length))

print('\x07')
toc = time.perf_counter()
print("%.1f seconds" % (toc - tic))

cv2.imwrite(os.path.splitext(FILENAME)[0] + "-out.png", result)


with open(os.path.splitext(FILENAME)[0] + ".py", "w") as f:
    f.write("pin_sequence = ")
    f.write(str(line_sequence))

# Save data to NUCLEO board
save_path = "F:\\"
file_name = str(os.path.splitext(FILENAME)[0]+ ".py")
completeName = os.path.join(save_path, file_name)
print(completeName)
with open(completeName, "w") as f:
    f.write("pin_sequence = ")
    f.write(str(line_sequence))
